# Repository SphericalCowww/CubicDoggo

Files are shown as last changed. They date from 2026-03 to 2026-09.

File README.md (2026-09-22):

# Cubic Doggo: Homemade 12-DOF 4-Legged Robot Recipe

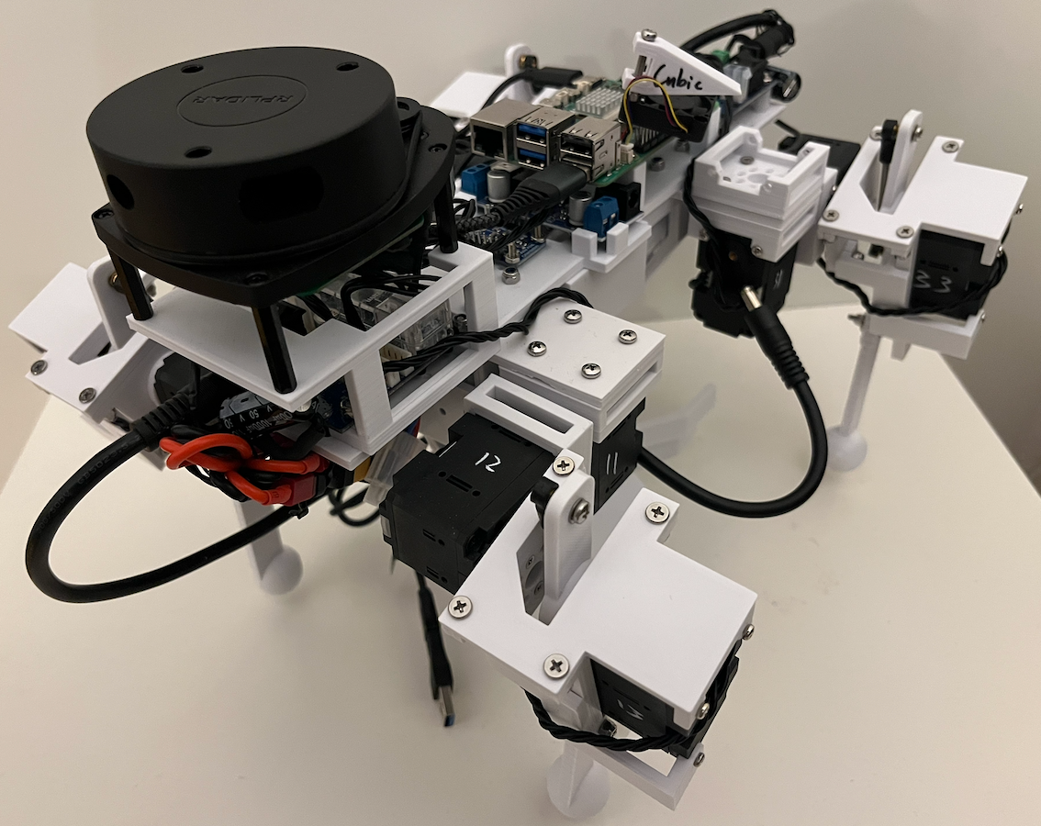
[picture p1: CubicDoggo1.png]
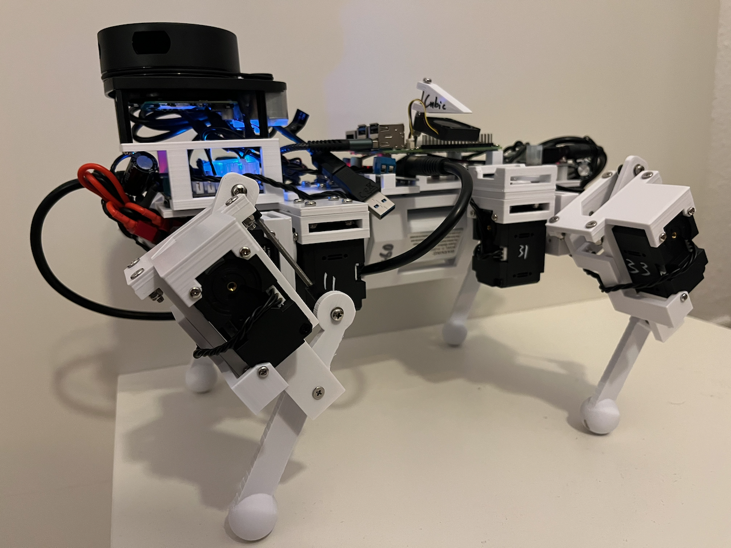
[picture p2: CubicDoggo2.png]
  

**Building from scratch a walking robot dog with all commercial/3D-printed parts and ROS2 Jazzy!**

Demos: derived from (<a href="https://github.com/SphericalCowww/ROS_leggedRobot_testBed">GitHub</a>/<a href="https://www.reddit.com/r/robotics/comments/1rouerc/first_time_building_a_hobbyist_robot_from_scratch/">Reddit</a>), upgrade in center of mass (<a href="https://www.reddit.com/r/ROS/comments/1roiee3/i_built_a_4legged_12dof_robot_dog_using_ros_2_i/">Reddit</a>), upgrade in walk gait (<a href="https://www.reddit.com/r/ROS/comments/1t8g1my/cubic_doggo_update_phew_it_finally_walks_with/">Reddit</a>), incorporate direction-turning in walk gait (<a href="https://www.reddit.com/r/robotics/comments/1tghftd/cubic_doggo_full_github_record_it_can_now_walk/">Reddit</a>/<a href="https://www.reddit.com/r/ROS/comments/1tghjte/cubic_doggo_full_github_record_it_can_now_walk/">Reddit</a>)

Overview: thanks to the Blue Robe AI channel <a href="https://www.youtube.com/watch?v=N3qaMB3oIC4">YouTube</a>.

Requirement: installing ROS2 Jazzy on a Raspberry Pi according to [GitHub](https://github.com/SphericalCowww/ROS_init_practice).

## Ingredients

### 3D printing

The 3D printer model VOXELAB Aquila X2 is used with the Cura slicer, but as long as PLA can be printed. All the FreeCAD files can be found here: <a href="https://github.com/SphericalCowww/CubicDoggo/tree/main/src/my_robot_description/mesh/CADv1">link</a>.

### Hardware requirements

| device | models | count | specification |
| - | - | - | - |
| servo motor | DYNAMIXEL <a href="https://emanual.robotis.com/docs/en/dxl/x/xl430-w250/">XL430-W250-T</a> | 12 | Max stall torque: 1.5 N*m (at 12.0V, 1.4A, 1.071 Nm/A). Weight of 57.2g. Need also corresponding signal wires of various lengths |
| USB communication interface | DYNAMIXEL <a href="https://emanual.robotis.com/docs/en/parts/interface/u2d2/">U2D2</a> | 1 | Can control 12 servo in daisy chain if properly powered |
| communication/power hub | DYNAMIXEL <a href="https://emanual.robotis.com/docs/en/parts/interface/u2d2_power_hub/">U2D2 power hub board</a> | 2 | Operating voltage	3.5-24V withg a maximum current	of 10A |
| onboard computer | Raspberry Pi 5 | 1 | For running just IK, a small RAM is sufficient; Pi 4 could be good enough as long as ROS2 Jazzy can be installed | 
| DC-DC step-down converter | Hailege <a href="https://www.amazon.de/Hailege-Module-Step-Down-Supply-Converter/dp/B07XFMMY1F">24V/12V to 5V/5A</a> | 1 | USB Port port to RaspPi,  DC 5.5mm x 2.5mm Male to battery | 
| battery | ZYGY <a href="https://www.amazon.de/dp/B0BB6RMM5Q">11.1V 2000mAh</a> | 2 | They already include protection. Need Charger. Need adapters for: T-plug => XT60 Male => DC 5.5mm x 2.5mm Male | 
| bearings | M3 bearing+<a href="https://www.amazon.de/dp/B01M2ZCLKX">spacer</a>, threaded rod, rod-end bearing | 8, 4, 4, 4 | rod length of 60mm to match the leg length; other dimensions can be accomodated by modifying the CAD |
| bolts and nuts | | | M3 screws are used throughout, except where required to accommodate the servos and electronic boards; use locknuts |

Other than the M3 screw, one specific requirement is the 12mm M2 screw (bag on the left in the photo) for the servo, which is not provided by the DYNAMIXEL package (bag on the right). Any shorter, the connection is too fragile, and any longer, the servo will be stuck from the inside. The M2.5 screws are generally provided by the DYNAMIXEL package, but other electrical boards may need them too, such as the RaspPi.

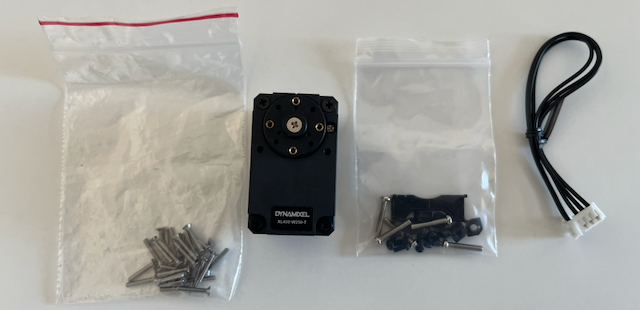
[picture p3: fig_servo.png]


Optional:

| device | models | count | specification |
| - | - | - | - |
| power supply | SMPS | 1 | 12V/5A for testing without batteries | 
| capacitor | 1000uF | 2 | rating 25V or higher | 

### Special soldering requirements

  * Solder two <a href="https://emanual.robotis.com/docs/en/dxl/x/xl320/#connector-information">MOLEX 51065-0300</a> cables together to form a Y-wire, otherwise U2D2 doesn't have enough connectors
  * Optional: connect a wire between the 2 U2D2 power hubs such that they have shared ground. Then solder a capacitor at each end to the power rail. Be careful about all the connection directions; otherwise, the whole power system can be severely damaged

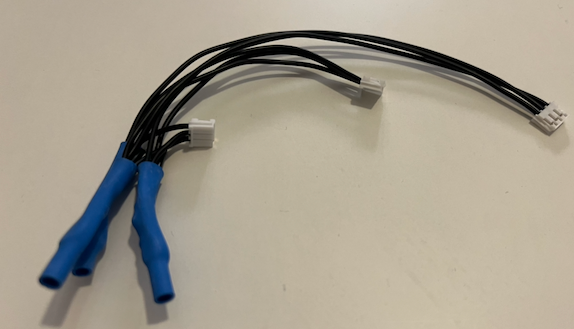
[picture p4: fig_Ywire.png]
  

### Power system

  * Daisy-chain no more than 3 servos to avoid delay
  * Power the hubs using their SMPS DC jacks. Then use the molex/screw terminal as an output to power the RaspPi via a ~12V-to-5V DC-DC converter
  * When powering the RaspPi with a DC-DC step-down converter, don't forget to put a kapton tape to insulate the two boards

 

### Tools used

There are quite a few screws in difficult locations with the current design, which may require several tools for full assembly and repair in a timely manner. The photo shows the tool used for this project.

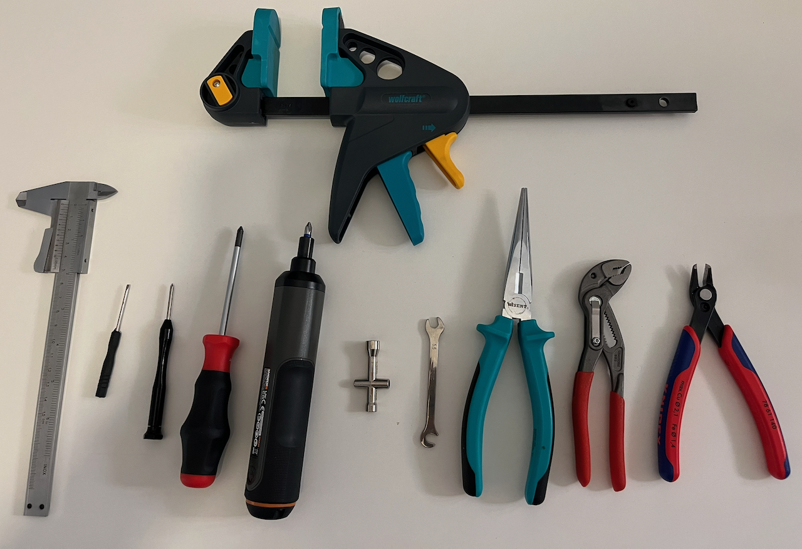
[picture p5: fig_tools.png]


## Running servos

### Setting the servo IDs

Connecting servo to U2D2 according to <a href="https://www.youtube.com/watch?v=FIj_NULYOKQ">YouTube</a>:



Use the following App <a href="https://emanual.robotis.com/docs/en/software/dynamixel/dynamixel_wizard2/">DYNAMIXEL Wizard 2.0</a> to change the servo ID (default 1) to, say, ID 10. Note that if any of the servos have the same ID, they will NOT show up in the scan. The servos also all initially come with an ID of 1, so they must be connected one by one to U2D2 to change their IDs accordingly.

    connect U2D2 to computer => open DYNAMIXEL Wizard 2.0
    # Options 
    ## Select protocol to scan => Protocol 2.0 (only)
    ## Select port to scan => which ever port is connected
    ## Select baudrate to scan => 57600 bps and 2000000bpt => OK
    ## Select ID range to scan => End => 50
    ## OK
    # Scan
    # Item 
    ## (Address 7) ID => ID 11 (on the right) => Save (may need to scroll down) 
    ## (Address 8) Baud Rate (Bus) => 2Mbps (on the right) => Save (may need to scroll down) 
    ## (Address 9) Return Delay Time => 0 (on the right) => Save (may need to scroll down) 
    ## (Address 68) Status Return Level => 2 (on the right) => Save (may need to scroll down) 

Can also test out the servo:

    # LED (top right toggle)
    # Torque (top right toggle) => set the value for motion (can select Velocity/Position mode)

For the 12 servos, the IDs are set as 11, 12, 13, 21, 22, 23, 31, 32, 33, 41, 42, and 43.

### Installing the <a href="https://github.com/ROBOTIS-GIT/DynamixelSDK">dynamixel-sdk</a> and <a href="https://github.com/ROBOTIS-GIT/dynamixel-workbench">dynamixel-workbench</a>

To install drivers for Dynamixel, 

    sudo apt install ros-jazzy-dynamixel-sdk* ros-jazzy-dynamixel-hardware* ros-jazzy-dynamixel-workbench*
    dpkg -l | grep dynamixel
    ros2 pkg list | grep dynamixel

Clone this repository,

    git clone https://github.com/SphericalCowww/CubicDoggo.git
    cd CubicDoggo

Then connect U2D2 to the RaspPi USB port. To check if ROS2 sees the servos: 

    cd CubicDoggo
    colcon build
    source install/setup.bash
    sudo dmesg | tail -n 20
    # look for:
    ## usb 2-2: Detected FT232H
    ## usb 2-2: FTDI USB Serial Device converter now attached to ttyUSB0
    ls -l /dev/ttyUSB*
    sudo chmod a+rw /dev/ttyUSB0                   # required everytime after reconnection
    ros2 run my_toolbox_dynamixel_workbench model_scan /dev/ttyUSB0 2000000
    ros2 run my_toolbox_dynamixel_workbench position /dev/ttyUSB0 2000000 11 0.5

Check <a href="https://github.com/SphericalCowww/ROS_leggedRobot_testBed">ROS_leggedRobot_testBed GitHub</a>, specifically <a href="https://github.com/SphericalCowww/ROS_leggedRobot_testBed/blob/main/src/my_robot_firmware/src/testRaspPi5_dynamixel_u2d2_channel0_xl430.cpp">firmware code</a> for more single servo application. However, do NOT run it on a connected robot. 

### Setting the latency

Update USB port latency to 1 ms. Note that this USB signal is delicate; use the shortest, highest-quality USB cable possible.: 

    lsusb
    # look for: Bus 002 Device 003: ID 0403:6014 Future Technology Devices International, Ltd FT232H Single HS USB-UART/FIFO IC
    sudo vim /etc/udev/rules.d/99-dynamixel-latency.rules
    ---------- add: 
    SUBSYSTEM=="tty", ATTRS{idVendor}=="0403", ATTRS{idProduct}=="6014", ATTR{device/latency_timer}="1", SYMLINK+="ttyU2D2", MODE="0666", GROUP="dialout"
    # ATTR{device/latency_timer}="1": Sets the 1ms latency (The "Sync Read" fix).
    # SYMLINK+="ttyU2D2": (Optional but helpful) This creates a static name for your device. You can now use /dev/ttyU2D2 in your code instead of /dev/ttyUSB0, so it won't break if you plug in another USB device.
    # MODE="0666": Allows your ROS node to access the port without needing sudo.
    ---------- 
    sudo vim /etc/udev/rules.d/99-ftdi.rules
    ---------- add: 
    SUBSYSTEM=="usb", ATTR{idVendor}=="0403", ATTR{idProduct}==6014, MODE="0666", GROUP="dialout"
    SUBSYSTEM=="tty", ATTRS{idVendor}=="0403", ATTRS{idProduct}=="6014", MODE="0666", GROUP="dialout"
    # This gives the correct permission to the USB port in question, otherwise, whenever reconnected, needs to do: sudo chmod a+rw /dev/ttyUSB0
    ---------- 
    sudo udevadm control --reload-rules
    sudo udevadm trigger
    ls -l /dev/ttyU2D2
    # if doesn't exist, do: sudo apt remove brltty
    cat /sys/class/tty/ttyUSB0/device/latency_timer
    # which should show 1 for 1 ms

Update to run the firmware with proper permissions to avoid latency:

    # without sudo, we will see the following WARNING in ros2 launch:
    ## [ros2_control_node-2] [WARN] [1766867979.090889912] [controller_manager]: Could not enable FIFO RT scheduling policy: with error number <1> (Operation not permitted). See [https://control.ros.org/master/doc/ros2_control/controller_manager/doc/userdoc.html] for details on enabling real-time scheduling.
    # with sudo, we can do the following:
    ## sudo bash -c "source /opt/ros/jazzy/setup.bash; source install/setup.bash; ros2 launch my_robot_bringup my_robot.with_commander.launch.py"
    # however, eventually we want to run without sudo in case it messes up with other permissions:
    sudo addgroup realtime
    sudo usermod -a -G realtime $USER
    sudo vim /etc/security/limits.d/realtime.conf:
    ----------  add:
    @realtime soft rtprio 99
    @realtime soft priority 99
    @realtime soft memlock unlimited
    @realtime hard rtprio 99
    @realtime hard priority 99
    @realtime hard memlock unlimited
    ---------- 
    sudo reboot

## Running a leg

### Assembly and Launching URDF

The double-bearing design will need a spacer in between. A long M3 screw is used to join the 2 bearing and connect with a locknut on the other side. Also, make sure the linkage rods are of the same length after installing the rod bearings. Finally, remember to twist the servo cables to reduce the signal interference from the power lines.

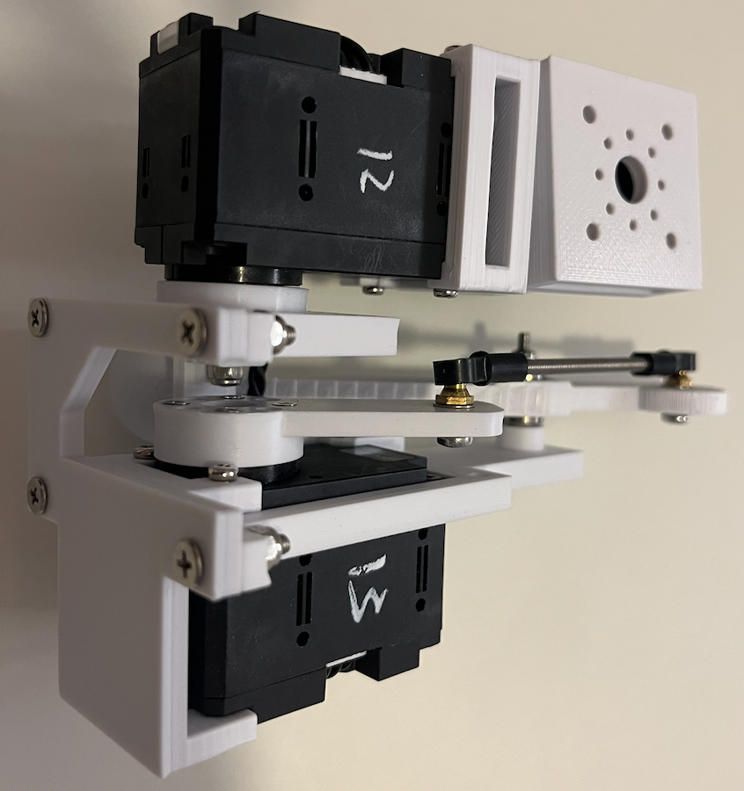
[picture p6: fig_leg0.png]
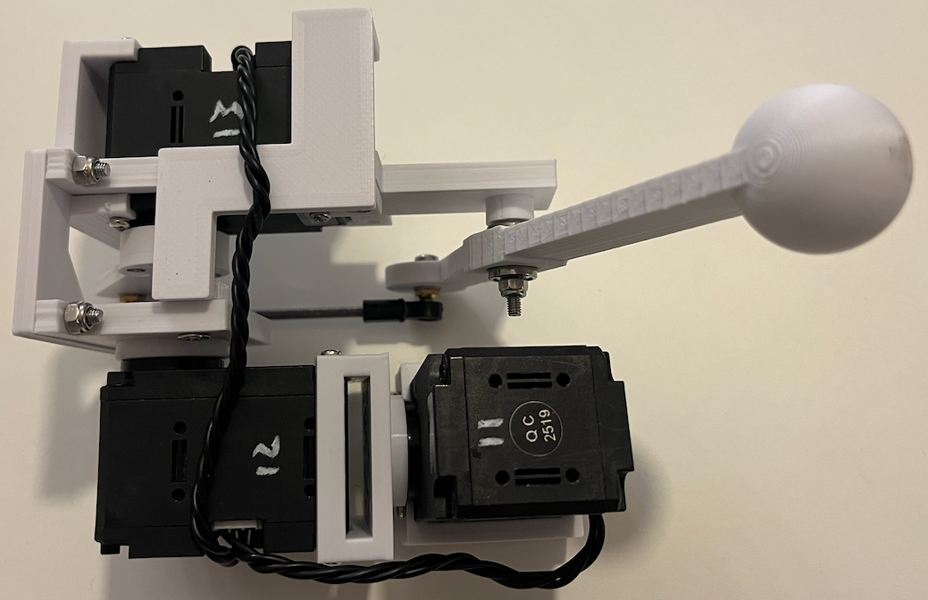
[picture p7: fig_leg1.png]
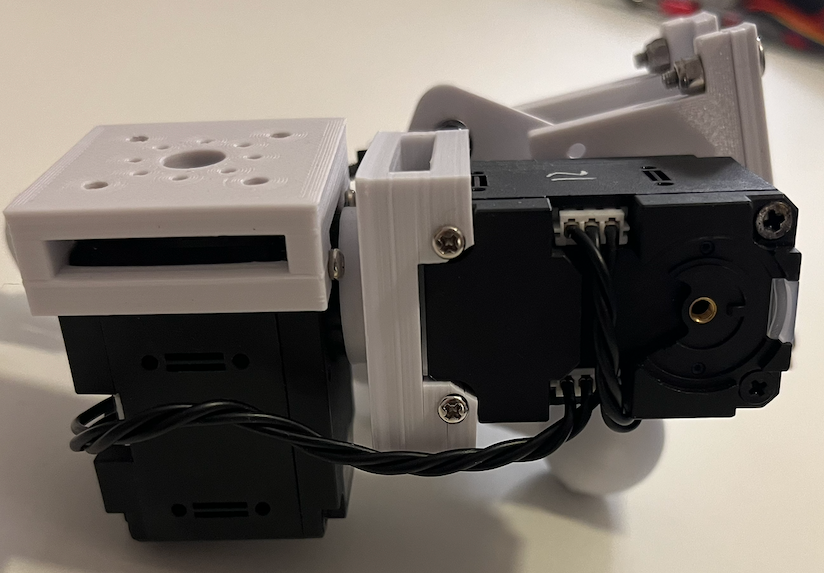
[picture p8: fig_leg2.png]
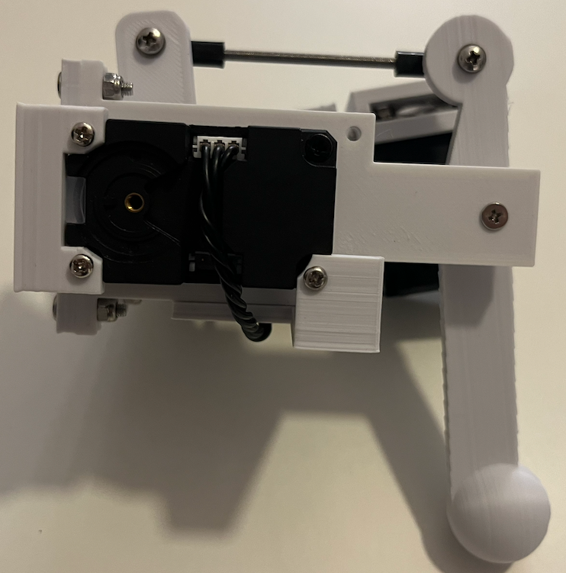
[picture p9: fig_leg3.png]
   

Run the following to view the moving parts:

    cd CubicDoggo
    colcon build
    source install/setup.bash
    ros2 launch my_robot_description my_robot.rviz.launch.xacro.py
    # if no config loaded
    ## Fixed Frame: base_link
    ## Add: RobotModel
    ## RobotModel: Description Topic: /robot_description

[Video demo](https://raw.githubusercontent.com/SphericalCowww/ROS_leggedRobot_testBed/main/rViz1Leg.mp4)

### Launching MoveIt2 demo:

    cd CubicDoggo
    colcon build
    source install/setup.bash
    ros2 launch my_robot_moveit_config demo.launch.py
    # ignore: [move_group-3] [ERROR] [1758361830.007872451] [move_group.moveit.moveit.ros.occupancy_map_monitor]: No 3D sensor plugin(s) defined for octomap updates
    # ignore: [rviz2-4] [ERROR] [1758361834.128908606] [moveit_143394722.moveit.ros.motion_planning_frame]: Action server: /recognize_objects not available
    # MotionPlanning:
    ## Planning Group: leg1
    ## Goal State: pose1
    ## Plan
    ## Execute

Note that to move the motion wheel in rViz:

    # toggle: Approx IK Solutions
    # toggle if needed: MotionPlanning => Planned Path => Loop Animation
    # toggle if needed: Use Cartesian Path 

If want to set up MoveIt2 from the beginning, check <a href="https://github.com/SphericalCowww/ROS_leggedRobot_testBed">GitHub</a> with ``moveit_setup_assistant``.

### Testing the ros2_control and MoveIt2

Under ``CubicDoggo/src/my_robot_description/urdf/my_robot.ros2_control.xacro``, 
   
   * use ``<plugin>mock_components/GenericSystem</plugin>`` if just want rViz
   * use ``<plugin>ma_robot_namespace::HardwareInterfaceU2D2_my_robot</plugin>`` if want to control hardware

Then run:
    
    cd CubicDoggo
    colcon build
    source install/setup.bash
    ros2 launch my_robot_bringup my_robot.with_lifecycle.launch.py
    # on another terminal
    ros2 topic pub -1 /leg1_set_named example_interfaces/msg/String "{data: "pose1"}"
    ros2 topic pub -1 /leg1_set_joint example_interfaces/msg/Float64MultiArray "{data: [3.14, 3.14, 3.14]}"
    ros2 topic pub -1 /leg1_set_pose my_robot_interface/msg/MyRobotLeg1PoseTarget "{x: -0.092, y: 0.053, z: 0.135, use_cartesian_path: false}" 
    ros2 service call /leg1_walk_toggle std_srvs/srv/SetBool "{data: true}"     # IK very easy to fail
    ros2 service call /leg1_walk_toggle std_srvs/srv/SetBool "{data: false}"
    ros2 lifecycle set /my_robot_lifecycle deactivate
    ros2 lifecycle set /my_robot_lifecycle shutdown

### Launching with launch file:

    cd CubicDoggo
    colcon build
    source install/setup.bash
    ros2 launch my_robot_bringup my_robot.launch.py
    # NOTE: Sometimes it takes a second try to have everything registered
    # Add => MotionPlanning
    ## Context => Planning Library => ompl
    ## Planning => Goal State: pose1 => Plan => Execute

## Running the full robot

### Assembly and Launching URDF

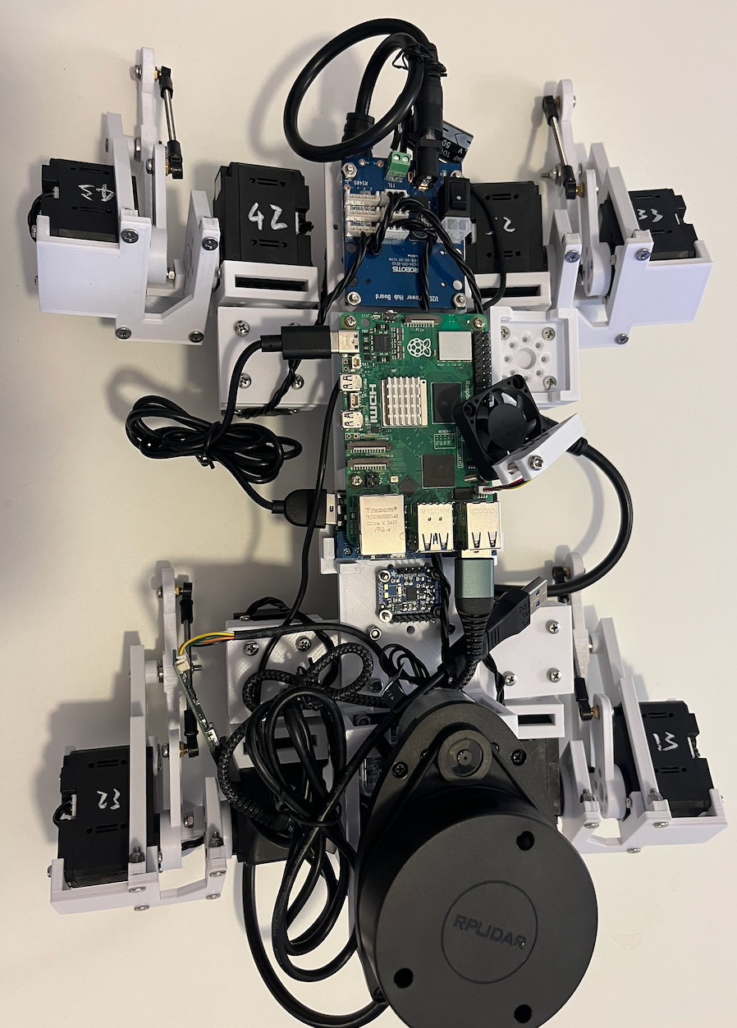
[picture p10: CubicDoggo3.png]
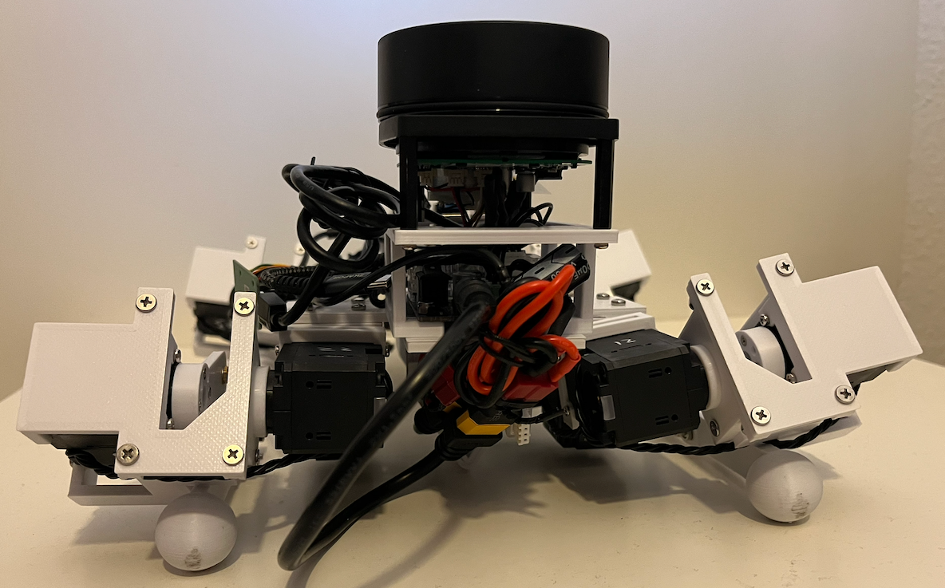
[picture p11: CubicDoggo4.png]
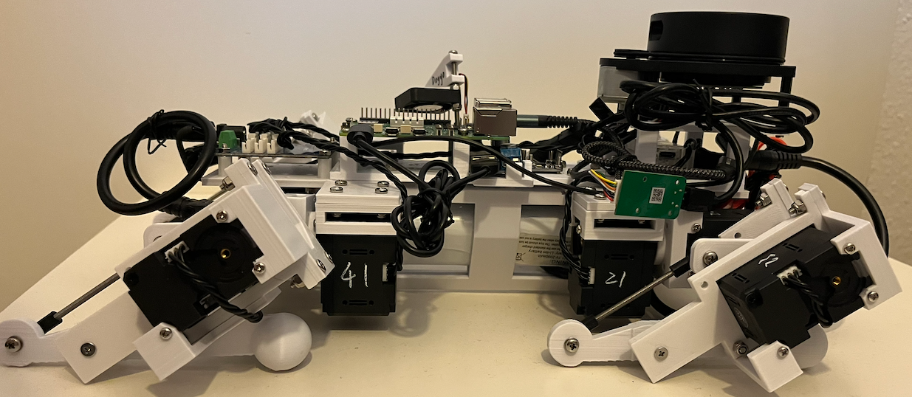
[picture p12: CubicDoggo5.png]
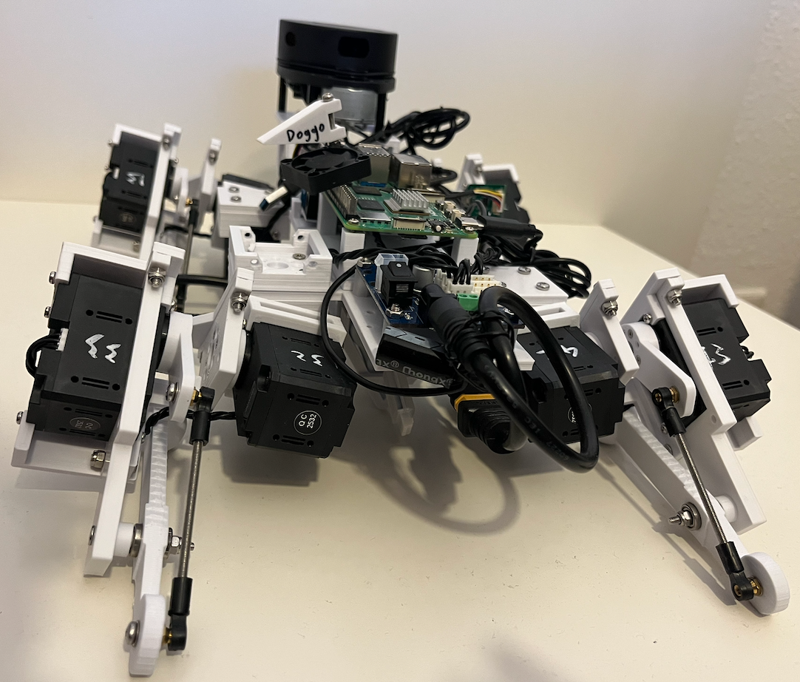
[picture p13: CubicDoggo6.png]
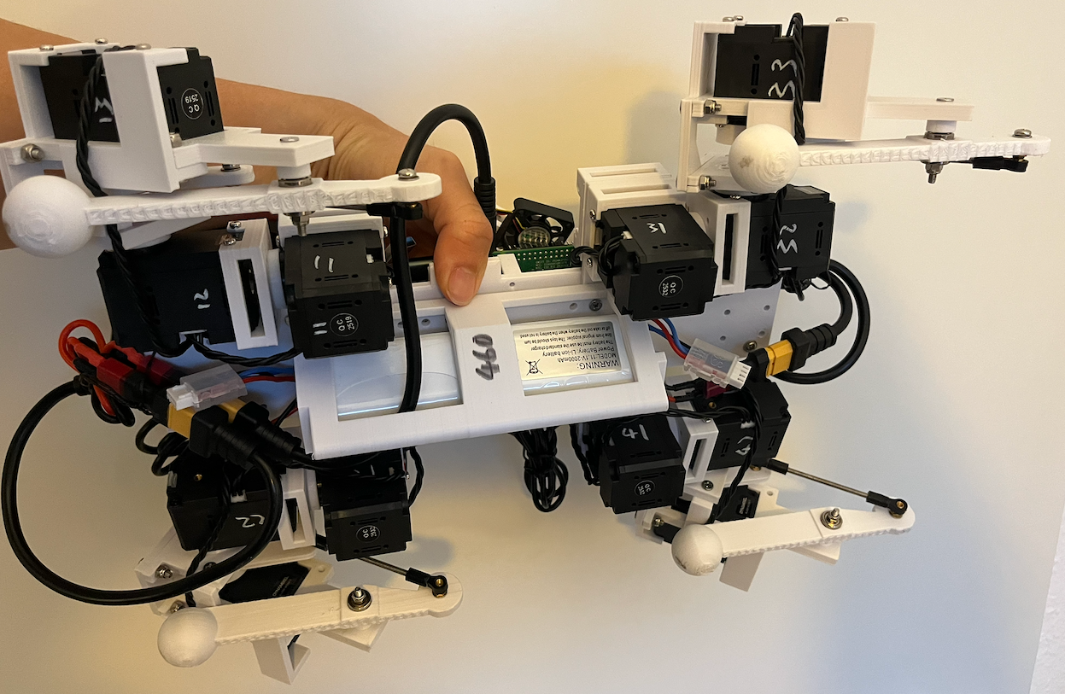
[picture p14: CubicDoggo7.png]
     

Run the following to view the moving parts:

    cd CubicDoggo
    colcon build
    source install/setup.bash
    ros2 launch my_robot_description cubic_doggo.rviz.launch.xacro.py

Notice that the placement of the first servo is different between the front and back legs.

### Launching with commands

Under: ``CubicDoggo/src/my_robot_description/urdf/cubic_doggo.ros2_control.xacro``

   * use ``<plugin>mock_components/GenericSystem</plugin>`` if just want rViz
   * use ``<<plugin>cubic_doggo_namespace/HardwareInterfaceU2D2_cubic_doggo</plugin>`` if want to control hardware

Under: ``CubicDoggo/src/my_robot_bringup/launch/cubic_doggo.with_lifecycle.launch.py``

   * comment out ``rviz_node`` if don't want rViz to show
   * comment out ``joy_driver_node`` and ``joy_controller_node`` if don't want the joystick controller
   * comment out ``peripheral_node`` if don't want warning from low power

Start the robot (skip launching rviz_node, joy_driver_node, or joy_controller_node if needed):

    cd CubicDoggo
    colcon build
    source install/setup.bash
    # comment in rvis node in CubicDoggo/src/my_robot_bringup/launch/cubic_doggo.with_lifecycle.launch.py
    ros2 launch my_robot_bringup cubic_doggo.with_lifecycle.launch.py
    # on another terminal
    ros2 topic pub -1 /leg_set_named example_interfaces/msg/String "{data: "rest"}"
    ros2 topic pub -1 /leg_set_named example_interfaces/msg/String "{data: "stand"}"
    ros2 topic pub -1 /leg_set_named example_interfaces/msg/String "{data: "sit"}"
    ros2 topic pub -1 /leg_set_named example_interfaces/msg/String "{data: "bow"}"
    ros2 topic pub -1 /leg_set_joint example_interfaces/msg/Float64MultiArray "{data: [0, 3.14, 3.14, 3.54]}"
    ros2 topic pub -1 /leg_set_pose my_robot_interface/msg/CubicDoggoLegPoseTarget "{leg_index: 0, x: -0.092, y: 0.053, z: 0.135}" 
    ros2 service call /leg_walk_toggle std_srvs/srv/SetBool "{data: true}"
    ros2 service call /leg_walk_toggle std_srvs/srv/SetBool "{data: false}"

Check out all the gait options under ``CubicDoggo/src/my_robot_commander/src/cubic_doggo_lifecycle.cpp``:

    # double maxVelScale = 1.0, maxAccScale = 1.0;
    # int    waypoint_N     = 100;       // number of waypoints for each cycle,      default 100
    # double waypoint_dt    = 0.01;      // second for each waypoint,                default 0.01
    # double IK_bufferTime  = 0.10;      // time at end of cycle buffer for IK calc, default 0.10
    # double swing_fraction = 0.50;      // creep < 0.25 < stable trot < 0.5 < trot
    # double lift = 0.02, x_stride_max = 0.02, y_stride_max = 0.025, x_shift = 0.0, y_shift = 0.0;
    # double x_stride = 0.0, y_stride = 0.0;

### Testing the joystick controller:

    ls /dev/input/js*
    # output: /dev/input/js0
    # otherwise do: sudo jstest /dev/input/js0
    ros2 run joy joy_enumerate_devices
    # if no device found
    sudo usermod -aG input $USER
    sudo reboot

    cd CubicDoggo
    colcon build
    source install/setup.bash
    ros2 run joy joy_node
    # on another terminal
    ros2 run my_robot_controller cubic_doggo_joy_control
    # on yet another terminal
    ros2 node info /cubic_doggo_joy_control    
    ros2 topic info /joy --verbose
    ros2 topic echo /joy

### Testing low power alarm

For the low RaspPi power alarm, it's set by the rasp_pi_peripheral_node:

    for d in /sys/class/hwmon/hwmon*; do echo -n "$d: "; cat "$d/name"; done   # find the correct path for power alarm
    # update /home/cubicdoggo/Documents/CubicDoggo/src/my_robot_bringup/launch/cubic_doggo.with_lifecycle.launch.py
    echo timer | sudo tee /sys/class/leds/ACT/trigger                          # trigger LED first
    sudo chmod -R 777 /sys/class/leds/ACT/                                     # enable LED to indicate battery condition
    # test the node if needed
    ros2 run my_robot_commander rasp_pi_peripheral_node --ros-args -p power_path:=$(which ever power alarm path)
    # create a fake alarm by
    echo 1 > /tmp/fake_alarm
    
### Launching at the start of RaspPi

    chmod +x /home/cubicdoggo/Documents/CubicDoggo/start_robot.sh
    sudo cp /home/cubicdoggo/Documents/CubicDoggo/robot_startup.service /etc/systemd/system/robot_startup.service
    sudo chmod 644 /etc/systemd/system/robot_startup.service
    sudo systemctl enable robot_startup.service                                # now will start at reboot
    sudo systemctl daemon-reload                                               # reload whenever there is a change
    # sudo systemctl restart robot_startup.service                             # restart, even if is rrunning
    # sudo systemctl stop    robot_startup.service                             # stop right now, kill all relevant nodes
    # sudo systemctl disable robot_startup.service                             # disable at reboot
    # journalctl -u robot_startup.service -n 100 > start_robot_output.txt      # to check the output
    # journalctl -u robot_startup.service -f

## Next directions

- <a href="https://github.com/SphericalCowww/CubicDoggo_06R">Cubic Doggo 06R High Mobility</a>: mechanical improvement and IMU adaptation
- <a href="https://github.com/SphericalCowww/CubicDoggo_07B">Cubic Doggo 07B Wouf</a>: ST-3215-C018 servo adaptation (higher torque, cheaper, but harder to develop)
- <a href="https://github.com/SphericalCowww/CubicDoggo_06Z">Cubic Doggo 06Z Neucommu</a>: AI and simulation testbed for reinforcement learning

## Acknowledgements

- Some utility programs are adapted from the ROBOTIS DYNAMIXEL Workbench examples: https://github.com/ROBOTIS-GIT/dynamixel-workbench/tree/main/dynamixel_workbench_toolbox/examples/src. These files remain licensed under the Apache License 2.0. Modifications are documented in the source files.

- Thanks to my second brother, who is a mechanical engineer, for advising me to use the locknuts, all-directional bearings, and battery for RC boats, as well as buying me a bunch of screws for cheap.

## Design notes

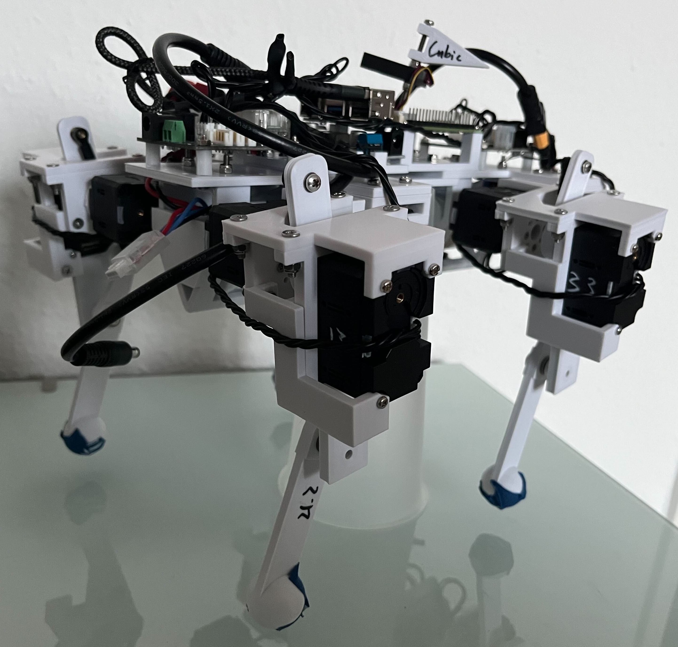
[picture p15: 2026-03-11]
CubicDoggo.png

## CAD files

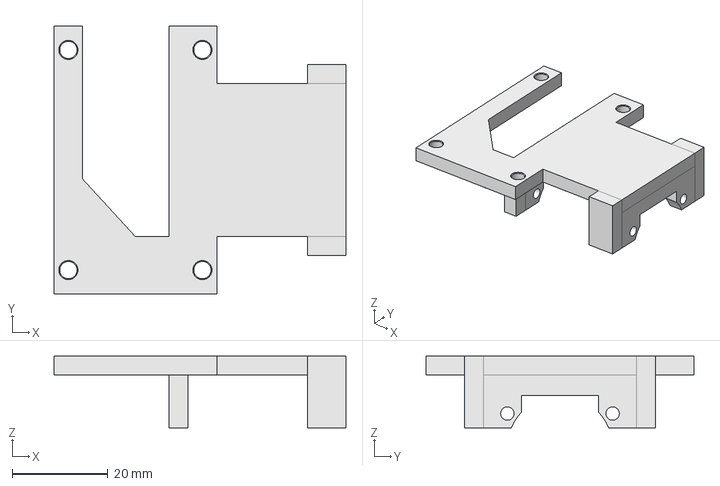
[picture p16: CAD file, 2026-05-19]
src/my_robot_description/mesh/CADv1/XL430holderThighFront.FCStd
61.0 x 56.0 x 15.0 mm

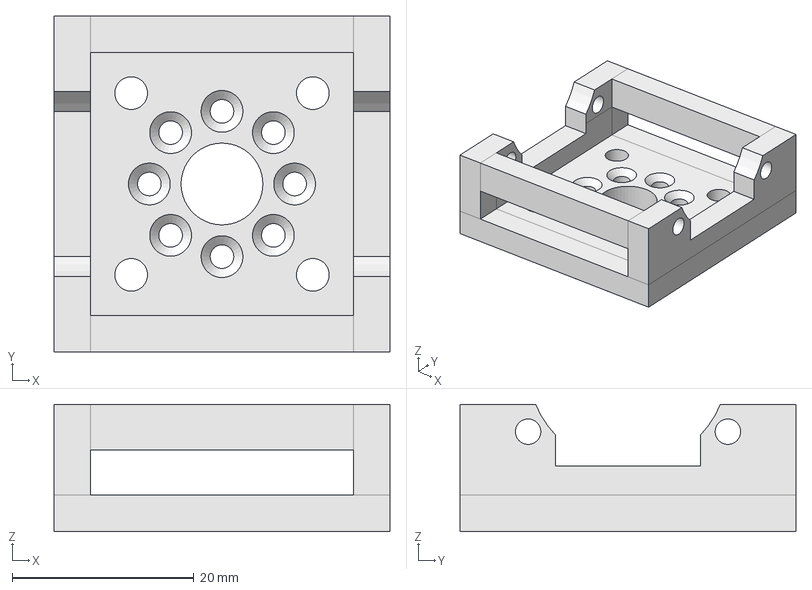
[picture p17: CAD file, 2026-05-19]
src/my_robot_description/mesh/CADv1/XL430holderBasic.FCStd
37.0 x 37.0 x 14.0 mm

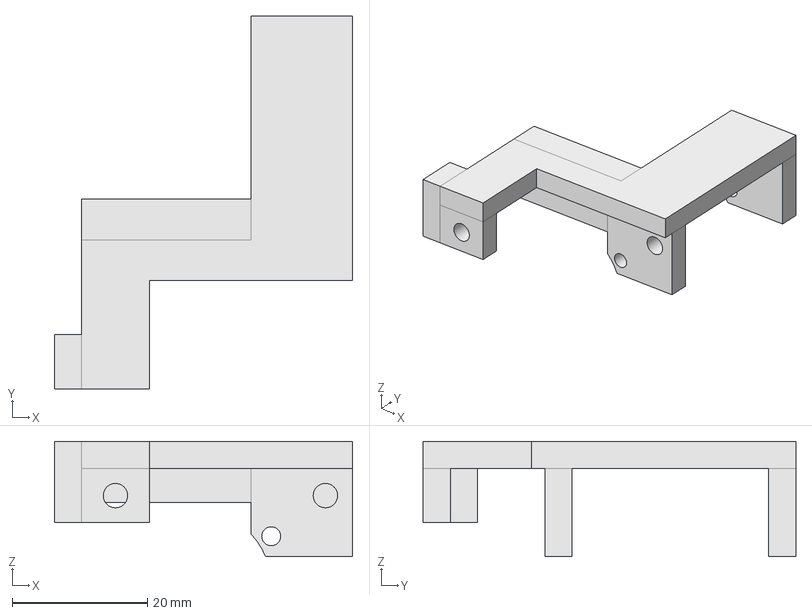
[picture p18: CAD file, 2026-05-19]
src/my_robot_description/mesh/CADv1/XL430holderThighBack.FCStd
44.0 x 55.0 x 17.0 mm

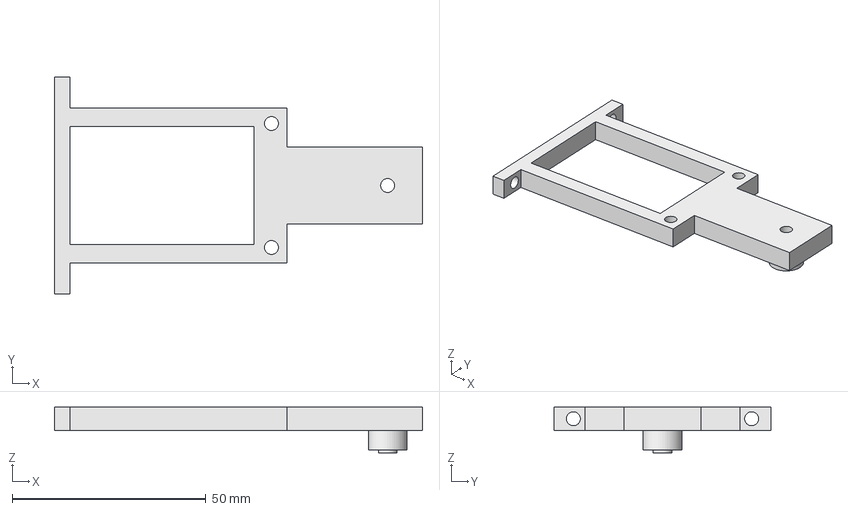
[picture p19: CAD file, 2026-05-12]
src/my_robot_description/mesh/CADv1/thighOuter.FCStd
95.0 x 56.0 x 11.8 mm

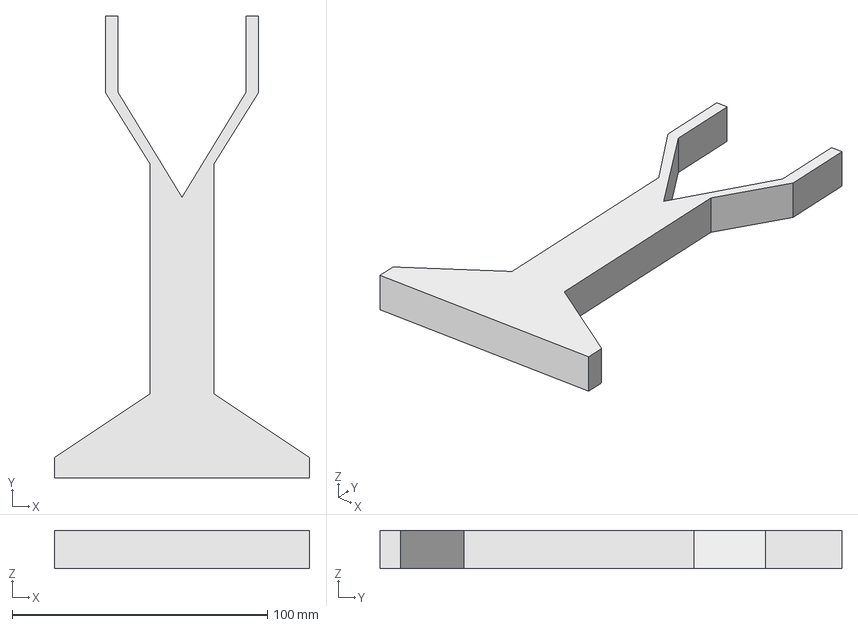
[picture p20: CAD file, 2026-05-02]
src/my_robot_description/mesh/CADv1/bodyHolder.FCStd
100.0 x 181.0 x 15.0 mm

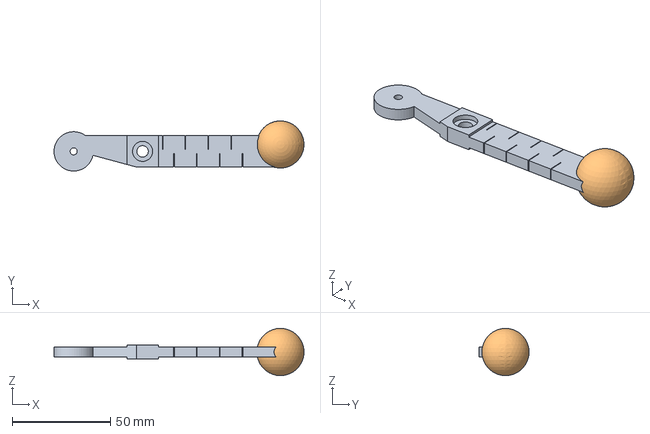
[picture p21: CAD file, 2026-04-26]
src/my_robot_description/mesh/CADv1/calfFeetSpring.FCStd
127.0 x 25.5 x 24.0 mm

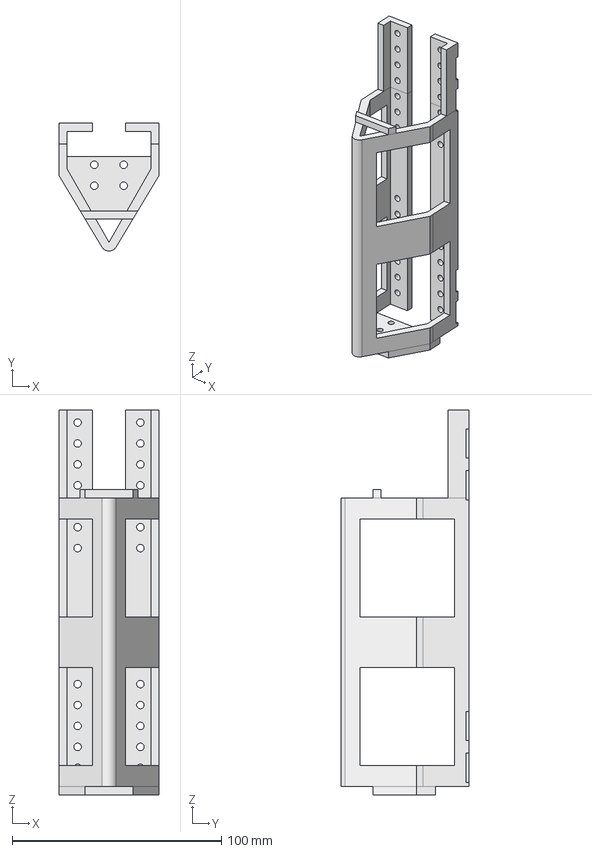
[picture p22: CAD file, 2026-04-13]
src/my_robot_description/mesh/CADv1/batteryHolder.FCStd
48.0 x 61.2 x 184.0 mm

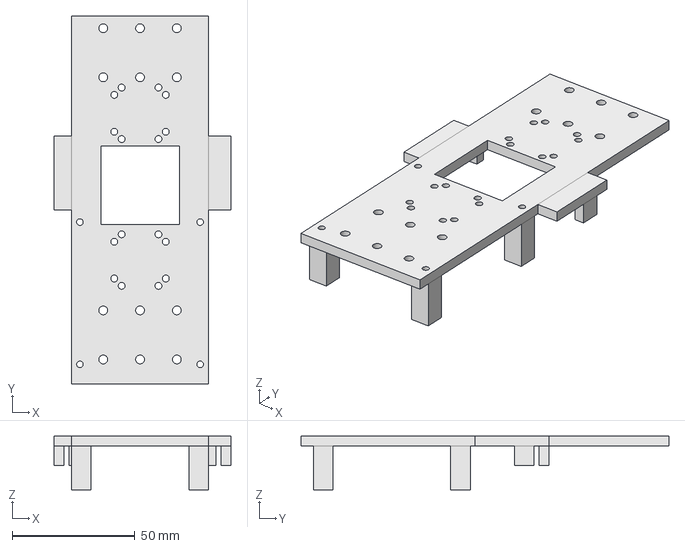
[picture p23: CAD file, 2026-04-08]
src/my_robot_description/mesh/CADv1/baseTorso.FCStd
72.0 x 150.0 x 22.0 mm

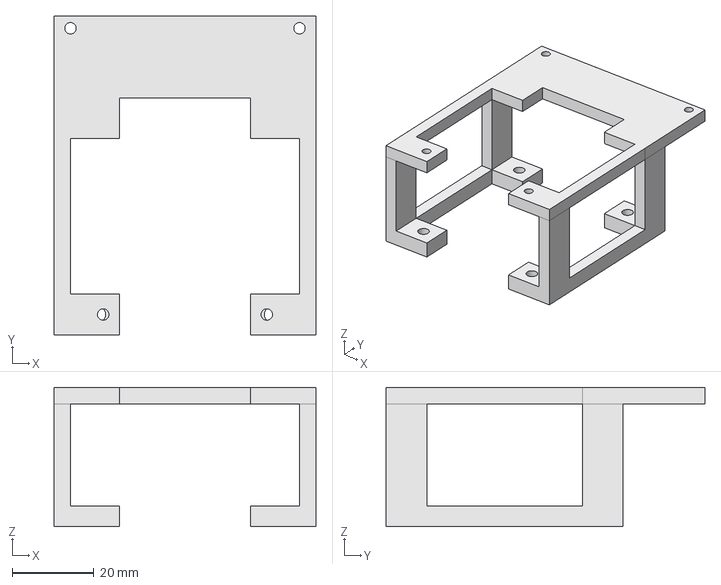
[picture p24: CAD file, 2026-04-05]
src/my_robot_description/mesh/CADv1/lidarHolder.FCStd
64.0 x 78.0 x 34.0 mm

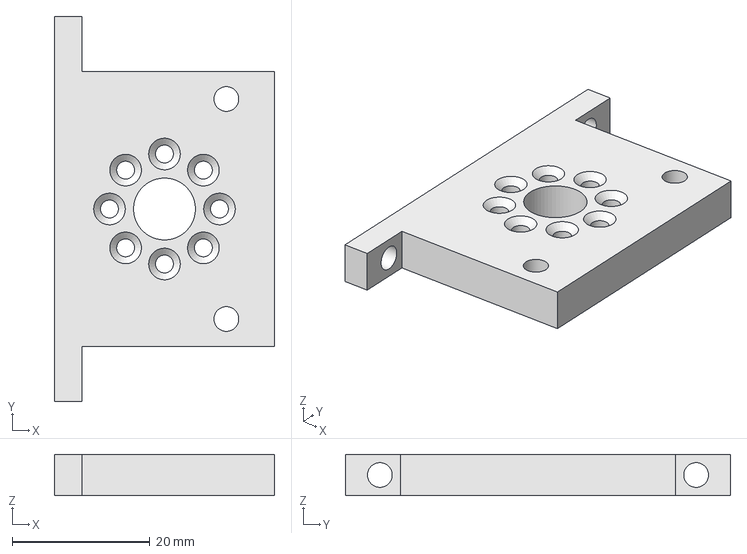
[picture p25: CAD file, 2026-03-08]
src/my_robot_description/mesh/CADv1/thighInner.FCStd
32.0 x 56.0 x 6.00 mm

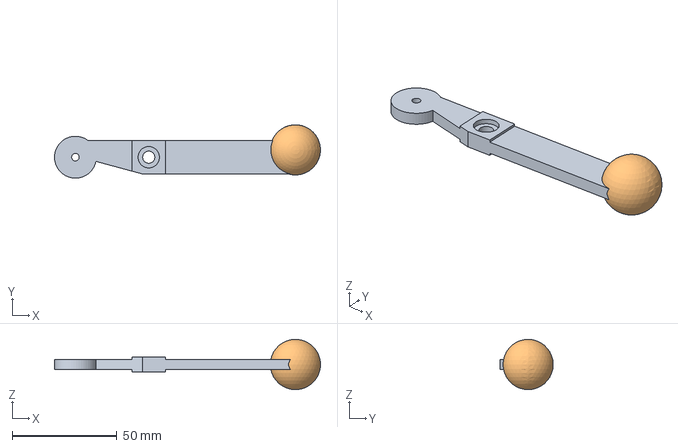
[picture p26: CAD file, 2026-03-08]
src/my_robot_description/mesh/CADv1/calfFeet.FCStd
127.0 x 25.5 x 24.0 mm

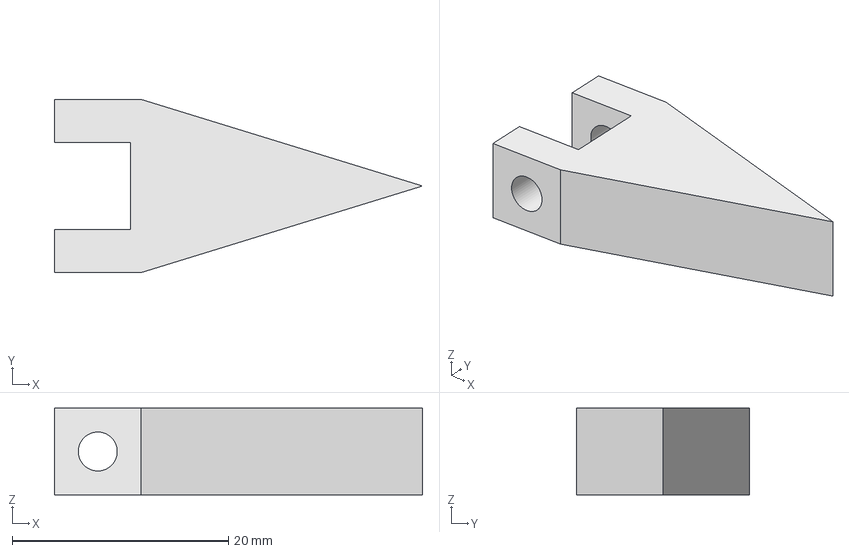
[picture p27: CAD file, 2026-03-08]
src/my_robot_description/mesh/CADv1/fanFlag.FCStd
34.0 x 16.0 x 8.00 mm

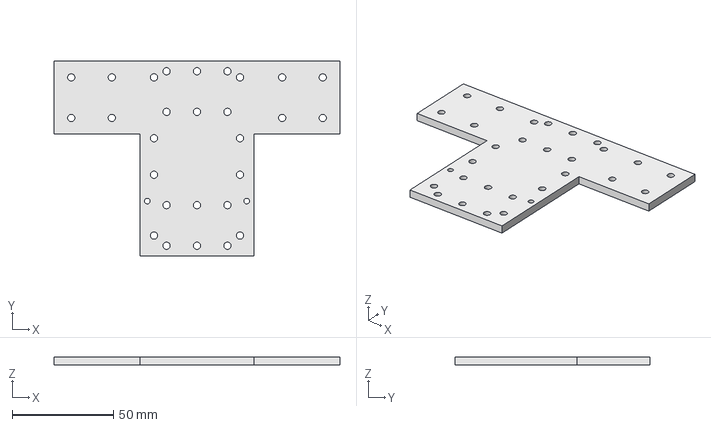
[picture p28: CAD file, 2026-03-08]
src/my_robot_description/mesh/CADv1/basePlate.FCStd
141.0 x 96.0 x 4.00 mm

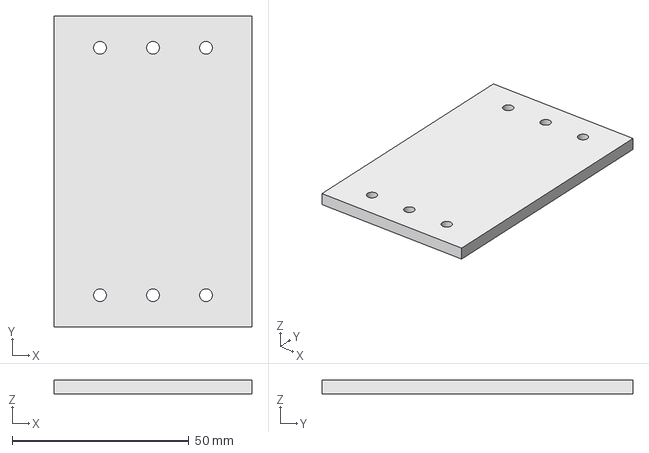
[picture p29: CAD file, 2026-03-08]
src/my_robot_description/mesh/CADv1/basePlateTorsoLower.FCStd
56.0 x 88.0 x 4.00 mm

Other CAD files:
src/my_robot_description/mesh/CADv1/calfJoint.FCStd
src/my_robot_description/mesh/CADv1/XL430rotorPadding.FCStd
src/my_robot_description/mesh/CADv1/XL430holderBasic.stl
src/my_robot_description/mesh/CADv1/basePlate.stl
src/my_robot_description/mesh/CADv1/baseTorso.stl
src/my_robot_description/mesh/CADv1/calfFeet.stl
src/my_robot_description/mesh/CADv1/calfJoint.stl
src/my_robot_description/mesh/CADv1/thighInner.stl
src/my_robot_description/mesh/CADv1/thighOuter.stl

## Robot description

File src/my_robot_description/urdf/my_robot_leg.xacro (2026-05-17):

<?xml version="1.0"?>
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
<robot xmlns:xacro="http://www.ros.org/wiki/xacro" name="my_robot_leg">
    <xacro:property name="servo_x" value="0.0285"/>
    <xacro:property name="servo_y" value="0.0465"/>
    <xacro:property name="servo_z" value="0.034"/>

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
    <link name="world"/>

    <link name="base_link">
        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
        <xacro:lazy_inertia m="10.0"/>
    </link>
    <joint name="world_base_link" type="fixed">
        <parent link="world"/>
        <child link="base_link"/>
    </joint>

    <link name="main_board">
        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
        <xacro:lazy_inertia m="0.0336"/>
    </link>
    <joint name="base_link_main_board" type="fixed">
        <parent link="base_link"/>
        <child link="main_board"/>
        <origin xyz="0 0.012 -0.004" rpy="0 0 0"/>
    </joint>

    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
    <link name="servo1_holder">
        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
        <xacro:box_inertia m="0.0098" x="0.037" y="0.037" z="0.014" o_xyz="0 0 0.007" o_rpy="0 0 ${urdf_pi/2}"/>
    </link> 
    <joint name="main_board_servo1_holder" type="fixed">
        <parent link="main_board"/>
        <child link="servo1_holder"/>
        <origin xyz="-0.050 0.018 0.004" rpy="0 0 0"/>
    </joint>   
 
    <link name="servo1">
        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
        <xacro:box_inertia m="0.0572" x="${servo_x}" y="${servo_y}" z="${servo_z}" o_xyz="0 0 ${servo_y/2}" o_rpy="${urdf_pi/2} 0 0"/>
    </link> 
    <joint name="servo1_holder_servo1" type="fixed">
        <parent link="servo1_holder"/>
        <child link="servo1"/>
        <origin xyz="0 0 0.008" rpy="0 0 0"/>
    </joint>

    <link name="servo1_padding">
        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
        <xacro:cylinder_inertia m="0.0013" r="0.011" l="0.004" o_xyz="0 -0.002 0" o_rpy="${urdf_pi/2} 0 0"/>
    </link> 
    <joint name="servo1_servo1_padding" type="revolute">
        <parent link="servo1"/>
        <child link="servo1_padding"/>
        <origin xyz="0 ${-servo_z/2-0.002} ${0.01+0.0025/2}" rpy="0 0 0"/>
        <axis xyz="0 -1 0"/>
        <limit effort="1000.0" velocity="50.0" lower="${urdf_pi - urdf_pi/3}" upper="${urdf_pi + urdf_pi/3}"/>
        <dynamics friction="0.05" damping="0.1"/>
    </joint>

    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
    <link name="servo2_holder">
        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
        <xacro:box_inertia m="0.0098" x="0.037" y="0.037" z="0.014" o_xyz="0 -0.007 0" o_rpy="${urdf_pi/2} 0 0"/>
    </link> 
    <joint name="base_link_servo2_holder" type="fixed">
        <parent link="servo1_padding"/>
        <child link="servo2_holder"/>
        <origin xyz="0 -0.004 0" rpy="0 0 0"/>
    </joint>
    
    <link name="servo2">
        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
        <xacro:box_inertia m="0.0572" x="${servo_x}" y="${servo_y}" z="${servo_z}" o_xyz="0 ${-servo_y/2} 0" o_rpy="0 ${urdf_pi/2} 0"/>
    </link> 
    <joint name="servo2_holder_servo2" type="fixed">
        <parent link="servo2_holder"/>
        <child link="servo2"/>
        <origin xyz="0 -0.008 0" rpy="0 0 0"/>
    </joint>

    <link name="servo2_padding">
        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
        <xacro:cylinder_inertia m="0.0013" r="0.011" l="0.004" o_xyz="0.002 0 0" o_rpy="0 ${urdf_pi/2} 0"/>
    </link> 
    <joint name="servo2_servo2_padding" type="revolute">
        <parent link="servo2"/>
        <child link="servo2_padding"/>
        <origin xyz="${servo_z/2+0.002} -0.03525 0" rpy="0 0 0"/>
        <axis xyz="1 0 0"/>
        <limit effort="1000.0" velocity="50.0" lower="${urdf_pi - 2*urdf_pi/6 - urdf_pi/6}" upper="${urdf_pi + 2*urdf_pi/6 - urdf_pi/6}"/>
        <dynamics friction="0.05" damping="0.1"/>
    </joint>

    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
    <link name="inner_thigh">
        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
        <xacro:box_inertia m="0.0085" x="0.032" y="0.040" z="0.006" o_xyz="0.003 -0.016 0" o_rpy="${-urdf_pi/2} 0 ${-urdf_pi/2}"/>
    </link>
    <joint name="servo2_padding_inner_thigh" type="fixed">
        <parent link="servo2_padding"/>
        <child link="inner_thigh"/>
        <origin xyz="0.004 0.016 0" rpy="0 0 0"/>
    </joint>

    <link name="outer_thigh">
        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
        <xacro:box_inertia m="0.0113" x="0.040" y="0.032" z="0.006" o_xyz="0.003 -0.0475 0" o_rpy="${-urdf_pi/2} ${urdf_pi/2-urdf_pi/2} ${-urdf_pi/2}"/>
    </link>
    <joint name="inner_thigh_outer_thigh" type="fixed">
        <parent link="inner_thigh"/>
        <child link="outer_thigh"/>
        <origin xyz="0.028 0 0" rpy="0 0 0"/>
    </joint>

    <link name="servo3">
        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
        <xacro:box_inertia m="${0.0572+0.0113+0.0078}" x="${servo_x}" y="${servo_y}" z="${servo_z}" o_xyz="0 ${-servo_y/2} 0" o_rpy="0 ${urdf_pi/2} 0"/>
    </link>
    <joint name="outer_thigh_servo3" type="fixed">
        <parent link="outer_thigh"/>
        <child link="servo3"/>
        <origin xyz="${servo_y/2-0.006-0.0025} -0.004 0" rpy="0 0 0"/>
    </joint>

    <link name="calfFeet">
        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
        <xacro:box_inertia m="${0.0251-0.0080}" x="0.110" y="0.016" z="0.004" o_xyz="0 ${-0.008+0.008} ${0.035-0.050}" o_rpy="0 ${-urdf_pi/2} 0"/>
    </link>
    <joint name="servo3_calfFeet" type="revolute">
        <parent link="servo3"/>
        <child link="calfFeet"/>
        <origin xyz="${-servo_z/2-0.002-0.0025} ${-0.086+0.004} 0" rpy="0 0 0"/>
        <axis xyz="-1 0 0"/>
        <limit effort="1000.0" velocity="50.0" lower="${5*urdf_pi/8}" upper="${11*urdf_pi/8}"/>
        <dynamics friction="0.0128" damping="0.1"/>
    </joint>

    <link name="calfJoint">
        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
        <xacro:box_inertia m="${0.0047+0.0015}" x="0.022" y="0.053" z="0.007" o_xyz="-0.0005 0 0.0155" o_rpy="${urdf_pi/2} 0 ${-urdf_pi/2}"/>
    </link>
    <joint name="servo3_calfJoint" type="revolute">
        <parent link="servo3"/>
        <child link="calfJoint"/>
        <origin xyz="${-servo_z/2-0.002-0.0025} ${-0.01-0.0025/2-0.001} 0" rpy="0 0 0"/>
        <axis xyz="-1 0 0"/>
        <mimic joint="servo3_calfFeet" multiplier="1.0" offset="0.0"/>
        <limit effort="1000.0" velocity="50.0" lower="${5*urdf_pi/8}" upper="${11*urdf_pi/8}"/>
        <dynamics friction="0.0212" damping="0.1"/>
    </joint>

    <link name="calfSphere">
        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
        <xacro:sphere_inertia m="0.0080" r="0.011" o_xyz="0 0 0" o_rpy="0 0 0"/>
    </link>
    <joint name="calfFeet_calfSphere" type="fixed">
        <parent link="calfFeet"/>
        <child link="calfSphere"/>
        <origin xyz="0 0.004 ${-0.105+0.035}" rpy="0 0 0"/>
    </joint>
</robot>
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

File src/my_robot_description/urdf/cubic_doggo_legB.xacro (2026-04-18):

<?xml version="1.0"?>
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
<robot xmlns:xacro="http://www.ros.org/wiki/xacro">
    <xacro:macro name="doggo_legB" params="prefix">

    <xacro:property name="servo_x" value="0.0285"/>
    <xacro:property name="servo_y" value="0.0465"/>
    <xacro:property name="servo_z" value="0.034"/>
    <xacro:if value="${prefix == 'BL'}">
        <xacro:property name="rflc" value="-1"/>
        <xacro:property name="base_plate" value='base_plate_B'/>
        <xacro:property name="servo1_holder_xyz" value=" 0.052 0.018 0.004"/>
    </xacro:if>
    <xacro:if value="${prefix == 'BR'}">
        <xacro:property name="rflc" value=" 1"/>
        <xacro:property name="base_plate" value='base_plate_B'/>
        <xacro:property name="servo1_holder_xyz" value="-0.052 0.018 0.004"/>
    </xacro:if> 
    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
    <link name="servo1_holder_${prefix}">
        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
        <xacro:box_inertia m="0.0098" x="0.037" y="0.037" z="0.014" o_xyz="0 0 0.007" o_rpy="0 0 ${urdf_pi/2}"/>
    </link> 
    <joint name="base_plate_servo1_holder_${prefix}" type="fixed">
        <parent link="${base_plate}"/>
        <child link="servo1_holder_${prefix}"/>
        <origin xyz="${servo1_holder_xyz}" rpy="0 0 0"/>
    </joint>
    
    <link name="servo1_${prefix}">
        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
        <xacro:box_inertia m="0.0572" x="${servo_x}" y="${servo_y}" z="${servo_z}" o_xyz="0 0 ${servo_y/2}" o_rpy="${urdf_pi/2} 0 0"/>
    </link> 
    <joint name="servo1_holder_servo1_${prefix}" type="fixed">
        <parent link="servo1_holder_${prefix}"/>
        <child link="servo1_${prefix}"/>
        <origin xyz="0 0 0.008" rpy="0 0 0"/>
    </joint>

    <link name="servo1_padding_${prefix}">
        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
        <xacro:cylinder_inertia m="0.0013" r="0.011" l="0.004" o_xyz="0 -0.002 0" o_rpy="${urdf_pi/2} 0 0"/>
    </link> 
    <joint name="servo1_servo1_padding_${prefix}" type="revolute">
        <parent link="servo1_${prefix}"/>
        <child link="servo1_padding_${prefix}"/>
        <origin xyz="0 ${-servo_z/2-0.002} ${0.01+0.0025/2}" rpy="0 0 0"/>
        <axis xyz="0 -1 0"/>
        <limit effort="1000.0" velocity="50.0" lower="${urdf_pi - urdf_pi/3}" upper="${urdf_pi + urdf_pi/3}"/>
        <dynamics friction="0.05" damping="0.1"/>
    </joint>

    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
    <link name="servo2_holder_${prefix}">
        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
        <xacro:box_inertia m="0.0098" x="0.037" y="0.037" z="0.014" o_xyz="0 -0.007 0" o_rpy="${urdf_pi/2} 0 0"/>
    </link> 
    <joint name="base_link_servo2_holder_${prefix}" type="fixed">
        <parent link="servo1_padding_${prefix}"/>
        <child link="servo2_holder_${prefix}"/>
        <origin xyz="0 -0.004 0" rpy="0 0 0"/>
    </joint>
    
    <link name="servo2_${prefix}">
        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
        <xacro:box_inertia m="0.0572" x="${servo_x}" y="${servo_y}" z="${servo_z}" o_xyz="0 ${-servo_y/2} 0" o_rpy="0 ${rflc*urdf_pi/2} 0"/>
    </link> 
    <joint name="servo2_holder_servo2_${prefix}" type="fixed">
        <parent link="servo2_holder_${prefix}"/>
        <child link="servo2_${prefix}"/>
        <origin xyz="0 -0.008 0" rpy="0 0 0"/>
    </joint>

    <link name="servo2_padding_${prefix}">
        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
        <xacro:cylinder_inertia m="0.0013" r="0.011" l="0.004" o_xyz="${rflc*0.002} 0 0" o_rpy="0 ${urdf_pi/2} 0"/>
    </link> 
    <joint name="servo2_servo2_padding_${prefix}" type="revolute">
        <parent link="servo2_${prefix}"/>
        <child link="servo2_padding_${prefix}"/>
        <origin xyz="${rflc*(servo_z/2+0.002)} -0.01125 0" rpy="0 0 0"/>
        <axis xyz="${rflc} 0 0"/>
        <limit effort="1000.0" velocity="50.0" lower="${urdf_pi - 2*urdf_pi/6 + rflc*urdf_pi/6}" upper="${urdf_pi + 2*urdf_pi/6 + rflc*urdf_pi/6}"/>
        <dynamics friction="0.05" damping="0.1"/>
    </joint>

    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
    <link name="inner_thigh_${prefix}">
        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
        <xacro:box_inertia m="0.0085" x="0.032" y="0.040" z="0.006" o_xyz="${rflc*0.003} -0.016 0" o_rpy="${rflc*urdf_pi/2} 0 ${urdf_pi/2}"/>
    </link>
    <joint name="servo2_padding_inner_thigh_${prefix}" type="fixed">
        <parent link="servo2_padding_${prefix}"/>
        <child link="inner_thigh_${prefix}"/>
        <origin xyz="${rflc*0.004} -0.016 0" rpy="0 0 0"/>
    </joint>

    <link name="outer_thigh_${prefix}">
        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
        <xacro:box_inertia m="0.0113" x="0.040" y="0.032" z="0.006" o_xyz="${rflc*0.003} 0.0475 0" o_rpy="${-urdf_pi/2} ${urdf_pi/2-rflc*urdf_pi/2} ${-rflc*urdf_pi/2}"/>
    </link>
    <joint name="inner_thigh_outer_thigh_${prefix}" type="fixed">
        <parent link="inner_thigh_${prefix}"/>
        <child link="outer_thigh_${prefix}"/>
        <origin xyz="${rflc*0.028} 0 0" rpy="${urdf_pi} 0 0"/>
    </joint>

    <link name="servo3_${prefix}">
        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
        <xacro:box_inertia m="${0.0572+0.0113+0.0078}" x="${servo_x}" y="${servo_y}" z="${servo_z}" o_xyz="0 ${-servo_y/2} 0" o_rpy="0 ${rflc*urdf_pi/2} 0"/>
    </link>
    <joint name="outer_thigh_servo3_${prefix}" type="fixed">
        <parent link="outer_thigh_${prefix}"/>
        <child link="servo3_${prefix}"/>
        <origin xyz="${rflc*(servo_y/2-0.006-0.0025)} -0.004 0" rpy="0 0 0"/>
    </joint>

    <link name="calfFeet_${prefix}">
        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
        <xacro:box_inertia m="${0.0251-0.0080}" x="0.110" y="0.016" z="0.004" o_xyz="0 ${-0.008+0.008} ${0.035-0.050}" o_rpy="0 ${-urdf_pi/2} 0"/>
    </link>
    <joint name="servo3_calfFeet_${prefix}" type="revolute">
        <parent link="servo3_${prefix}"/>
        <child link="calfFeet_${prefix}"/>
        <origin xyz="${rflc*(-servo_z/2-0.002-0.0025)} ${-0.086+0.004} 0" rpy="${urdf_pi} 0 0"/>
        <axis xyz="${-rflc} 0 0"/>
        <limit effort="1000.0" velocity="50.0" lower="${5*urdf_pi/8}" upper="${11*urdf_pi/8}"/>
        <dynamics friction="0.0128" damping="0.1"/>
    </joint>
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

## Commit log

2026-03-08 - copy all cubic_doggo related item from the other repository
    [XL430holderBasic.FCStd, XL430holderBasic.stl, XL430holderThighBack.FCStd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]
2026-03-15 - speeding up the motor vel/acc during the walk gait
    [joint_limits.yaml]
2026-03-24 - update the dimension of the new holders
    [batteryHolder.FCStd, lidarHolder.FCStd]
2026-04-02 - adding a holder to support the robot during test
    [batteryHolder.FCStd, bodyHolder.FCStd, lidarHolder.FCStd]
2026-04-05 - shifting center of mass does seems to help, so futher optimization
    [basePlateTorsoUpper.FCStd, basePlateTorsoUpper.stl, baseTorso.FCStd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]
2026-04-08 - some updates to CAD model again
    [baseTorso.FCStd, baseTorso.stl, batteryHolder.FCStd]
2026-04-10 - initial update for urdf with the new geometry
    [cubic_doggo.ros2_control.xacro, cubic_doggo.urdf.xacro, cubic_doggo_legB.xacro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]
2026-04-11 - the robot can now move correctly again with the updated urdf
    [cubic_doggo.ros2_control.xacro, cubic_doggo_leg.xacro, cubic_doggo_legB.xacro]
2026-04-12 - adding controller code
    [cubic_doggo.ros2_control.xacro]
2026-04-12 - updated to directly test the controller on the robot
    [cubic_doggo.ros2_control.xacro]
2026-04-13 - adding spring structure to the feet
    [batteryHolder.FCStd, calfFeetSpring.FCStd]
2026-04-14 - more stiff design for the spring leg; previous version too soft
    [calfFeetSpring.FCStd]
2026-04-14 - adding current limit and PID adjustment
2026-04-18 - adding gait function - adding a triangle gait
    [calfFeetSpring.FCStd]
2026-04-18 - gait code now compiles - differentiate PID for first servo as compared to the other two
2026-04-18 - debug IK solution not found, just stride/lift reversed - redon cubic_doggo_legB.xacro rigorously peice by peice
    [cubic_doggo_legB.xacro, cubic_doggo_legF.xacro]
2026-04-19 - adding jerk for smoothing: https://github.com/moveit/moveit2/blob/jazzy/moveit_core/trajectory_processing/include/moveit/trajectory_processing/ruckig_traj_smoothing.hpp
    [joint_limits.yaml]
2026-04-26 - hopefully, now the gait is slightly more state safe
    [bodyHolder.FCStd, calfFeetSpring.FCStd]
2026-05-02 - add a node for low battery detection
    [bodyHolder.FCStd]
2026-05-03 - power alarm node should work now
2026-05-04 - avoiding setDefaultVelAccScaler_(double velScale, double accScale) conflict with trajecotry solver - adding blinking on the servos if on low voltage => to be compiled and tested
2026-05-07 - 100 waypoint sin walk gait init
    [XL430holderThighBack.FCStd]
2026-05-08 - using joint publisher in attempt to combat "cycle boundary pauses". Need to be tested
2026-05-09 - adding swing_fraction to enable 4-phase walk gait to account for weaker legs
2026-05-09 - compile and run, but still need to test on ground
2026-05-10 - direction control appear to be working, will need to test if it walks on ground - reorganized a few of the gait parameters and concentrate them all in one place
2026-05-12 - updated the leg joint design after its snapping when overloaded. The new design no longer requires solding threaded inserts that needs constant retightening; locknuts are use on the other side inst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
    [thighOuter.FCStd]
2026-05-15 - initially adding files for 1leg tests
    [cubic_doggo.urdf, joint_limits.yaml, my_robot.ros2_control.xacro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]
2026-05-15 - quick changes
    [my_robot_leg.xacro]
2026-05-17 - one leg code now working again
    [my_robot_leg.xacro]
2026-05-17 - photos for 1 leg assembly
2026-05-19 - small change to reinenforce the places where cracks happen
    [XL430holderBasic.FCStd, XL430holderThighBack.FCStd, XL430holderThighFront.FCStd]
